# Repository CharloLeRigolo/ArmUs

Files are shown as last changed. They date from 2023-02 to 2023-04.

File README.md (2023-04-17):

# Table of content
- [ArmUs](#armus)
- [Accessing documentation](#accessing-documentation)
- [Setup](#setup)
  * [Setting up your environement (software)](#setting-up-your-environement-software)
  * [Material (Software side)](#material-software-side)
  * [Material and assembly](https://github.com/CharloLeRigolo/arm_us/tree/main/Mechanics)
- [Running the robot](#running-the-robot)
- [ROS information](#ros-information)
  * [General picture](#general-picture)
  * [Packages](#packages)
  * [Launch files](#launch-files)
  * [Config files](#config-files)
  * [Msg, srv and action files](#msg-srv-and-action-files)
- [License](#license)

# ArmUs
ArmUs is a 5 axis robot made to reproduce movement and goemetry of a real human arm. It's made by a team of 6 sherbrooke university undergraduates. The goal is to eventually add a robotic hand at the end and be able to control the whole arm-hand assembly by moving your arm. 

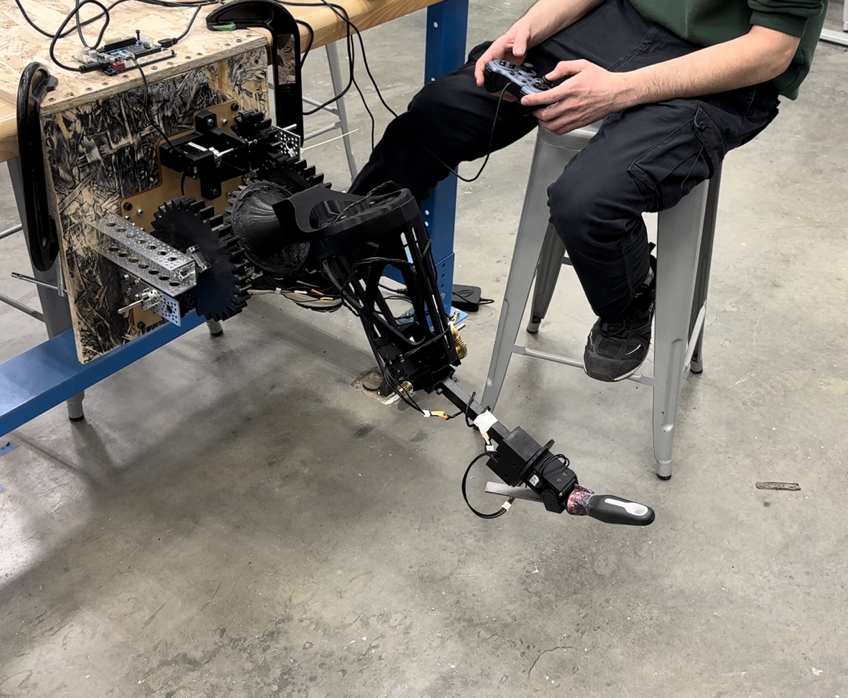
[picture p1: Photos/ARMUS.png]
ARM US


At this stage, the arm can be controled either in joint or in cartisian mode and can be visualized and calibrated in real time, it also supports software protection, torque limiters to reduce risks and a simulation mode for test purposes.

Control interface (HMI)
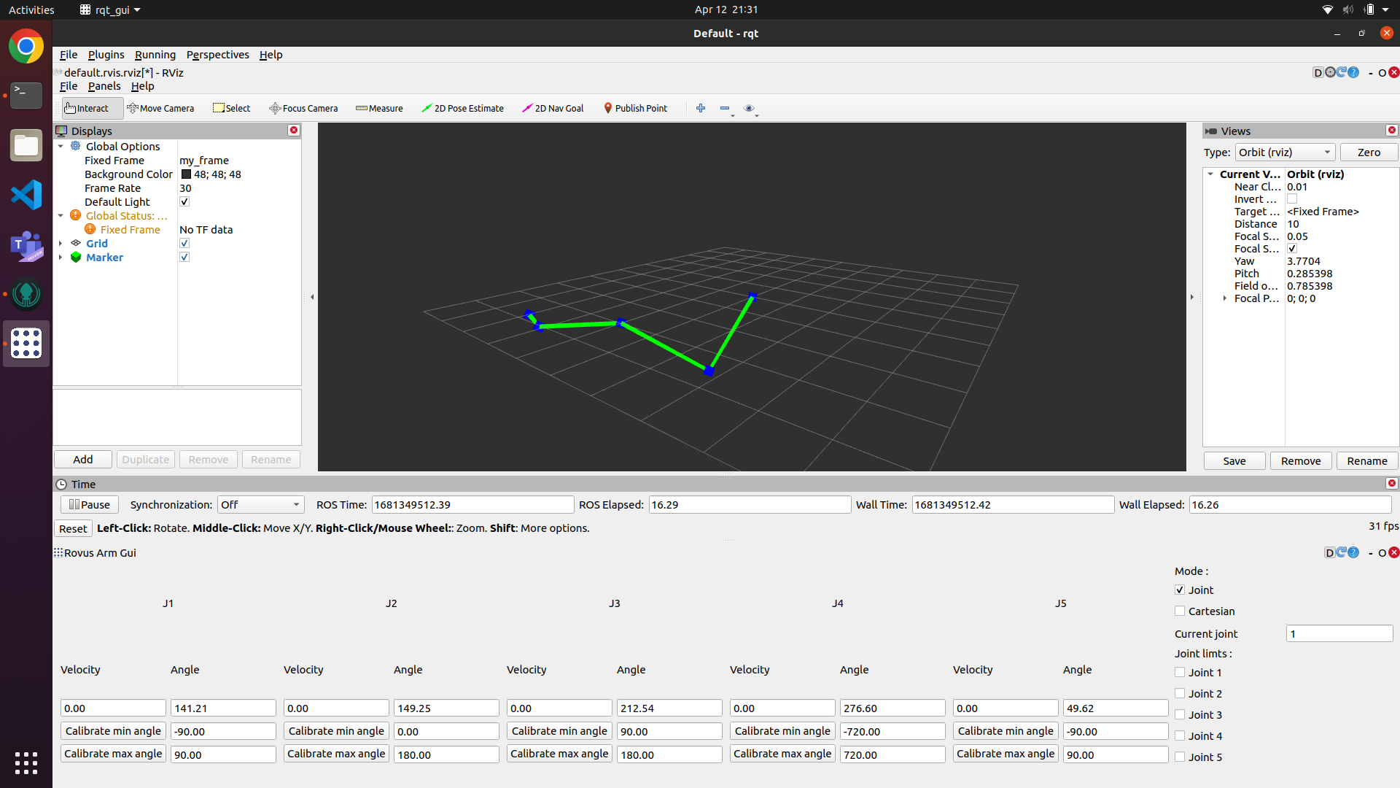
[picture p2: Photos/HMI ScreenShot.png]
HMI


# Accessing documentation
To open a package's documentation, open the index.html file found in it's "/doc" folder in your browser.
Ex:
```
firefox ~/catkin_ws/src/arm_us/arm_us/doc/html/index.html
```

# Setup
## Setting up your environement (software)
1.  Start by installing [ubuntu 20.04 desktop Focal Fossa](https://releases.ubuntu.com/focal/) on your machine (VM or dualboot), dualboot is highly recommended.
2.  Install ROS-Noetic by following [this tutorial](http://wiki.ros.org/noetic/Installation/Ubuntu)
3.  Edit your bashrc
    - Open your .bashrc (if you're using bash) 
      ```
      sudo nano ~/.bashrc
      ```
    - Then add these lines at the end
      ```
      source /opt/ros/noetic/setup.bash
      source ~/catkin_ws/devel/setup.bash
      ```
    - Save and exit
      ```
      ctrl+s
      ctrl+x
      ```
4.  Setup your catkin_ws by following [this tutorial](http://wiki.ros.org/ROS/Tutorials/InstallingandConfiguringROSEnvironment)
5.  Clone all the arm_us packages from this git repo to your catkin_ws/src folder
    - arm_us
    - arm_us_graph
    - gui_arm_us
    - arm_us_msg

6.  Install all the dependencies:
    - Dependencies
      - joy
      - dynamixel_sdk
      - dynamixel_interface

    - Run these commands to install packages available in rosdep:
      ```
      sudo apt install ros-noetic-joy
      ```

    - Some packages need to be cloned directly from GitHub as they aren't maintained in rosdep, to clone them,
      - first make */catkin_ws/src/* your working directory:
        ```
        cd ~/catkin_ws/src
        ```
      - Then, enter these commands to clone the packages:
        ```
        git clone https://github.com/csiro-robotics/dynamixel_interface.git
        git clone https://github.com/ROBOTIS-GIT/DynamixelSDK.git
        ```
    - Once all dependencies are installed, don't forget to compile your workspace
      ```
      cd ~/catkin_ws/
      catkin_make
      ```
7. Setup your OpenCR in bridge mode
	1. Install [ArduinoIDE](https://www.arduino.cc/en/software) on a computer
	2. Follow the steps in section 4.X (depending on your operating system) of the [ROBOTIS e-Manual for OpenCR](https://emanual.robotis.com/docs/en/parts/controller/opencr10/)
	3. Select the OpenCR board in ArduinoIDE
	4. Select "usb_to_dxl" In *File -> Examples -> OpenCR -> 10. Etc -> usb_to_dxl*
	5. Upload the example to the OpenCr board, make sure you're on the correct port and the device in /dev/ttyXXX has read/write access
		```
		sudo chmod a+rw /dev/ttyACM0
		```
	The OpenCR board is now in bridge mode. We will be able to control it directly from the Serial Port

## Material (Software side)
For the robot's assembly, follow the [README.md](https://github.com/CharloLeRigolo/arm_us/blob/main/Mechanics/README.md) in [/Mechanics](https://github.com/CharloLeRigolo/arm_us/tree/main/Mechanics).

- 1 OpenCR board
- 1 OpenCR 120VAC to 12VDC powersupply
- 2 Dynamixel XL430 motors
- 3 Dynamixel XM430 motors
- 1 USB micro B to USB A
- 1 Generic controller (any controller compatible with [joy](http://wiki.ros.org/joy) will work, you'll probably need to remap the keybindings if you're not using a logitech controller, in [/arm_us/config/controller_config.yaml](https://github.com/CharloLeRigolo/arm_us/blob/main/arm_us/config/controller_config.yaml)

# Running the robot
Open a terminal and launch the first launchfile:
```
roslaunch arm_us 1_interface.launch
```
This will start the HMI and the communication with the motors.
Calibrate the robot by following this [guide](https://github.com/CharloLeRigolo/arm_us/tree/main/arm_us/README.md).

Once ArmUs is calibrated, launch the 2nd launchfile
```
roslaunch arm_us 2_control.launch
```
This will enable the torque on the motors and enable the control with the controller, you should now be able to control the motors with your controller in joint or cartesian as you wish (see [keybinding]https://github.com/CharloLeRigolo/arm_us/blob/main/Photos/Keybindings%20Cartesian%20(En).PNG)

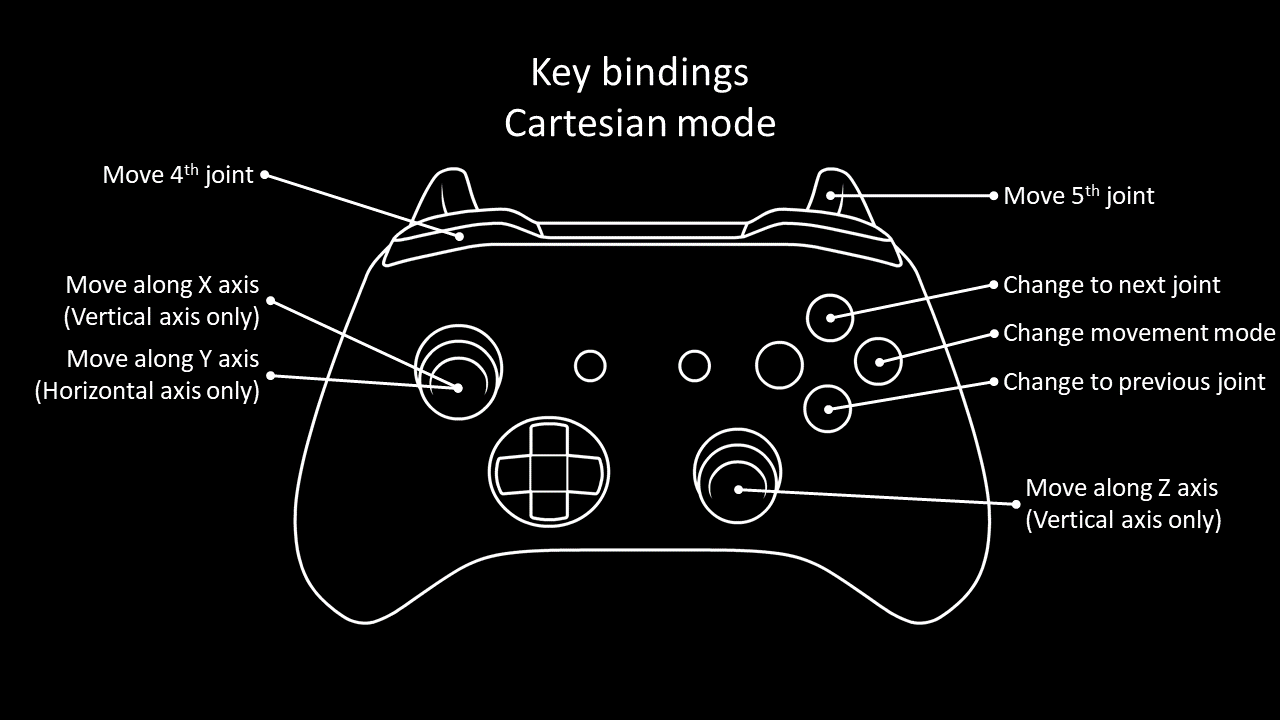
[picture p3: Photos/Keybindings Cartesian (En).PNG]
Joint control


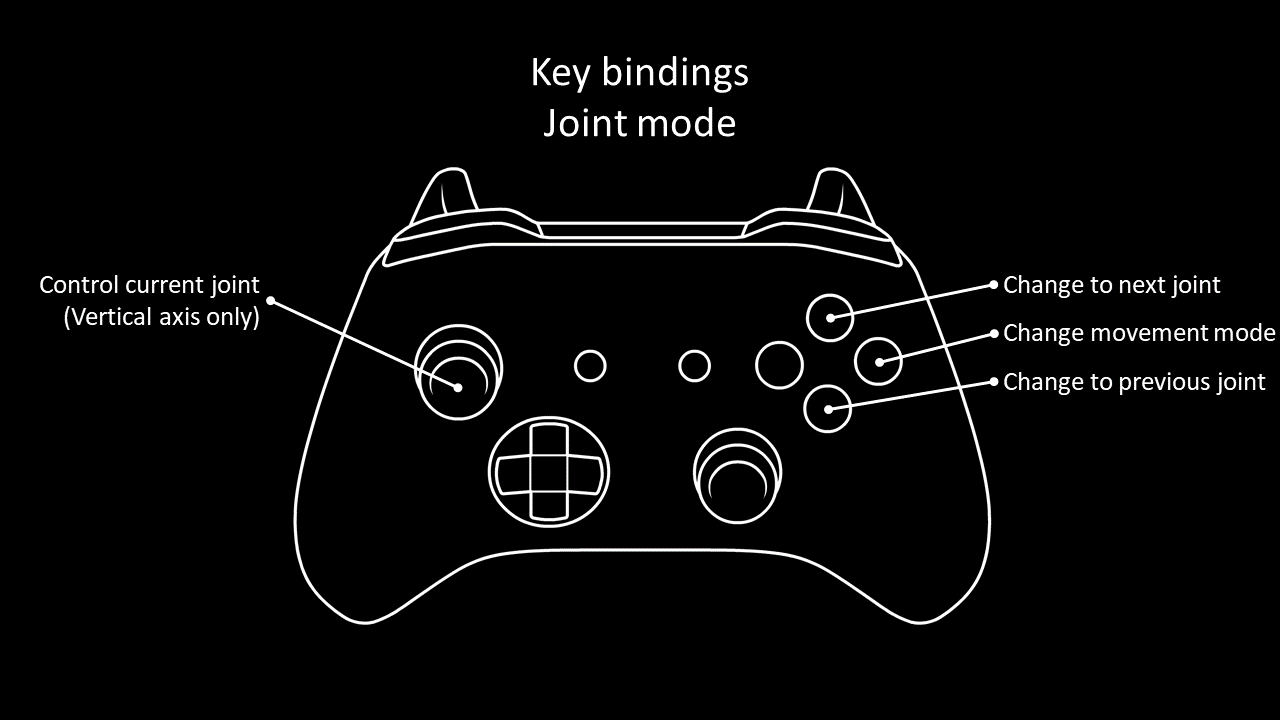
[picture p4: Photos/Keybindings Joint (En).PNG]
Cartesian control


Before killing your node, if you want to keep your calibration values, run this command
```
rosparam dump **yourpath**/calib.yaml
```
and copy the lines under "motor_translator:" in the config file arm_us/config/joint_limit.yaml.

# ROS information
## General picture
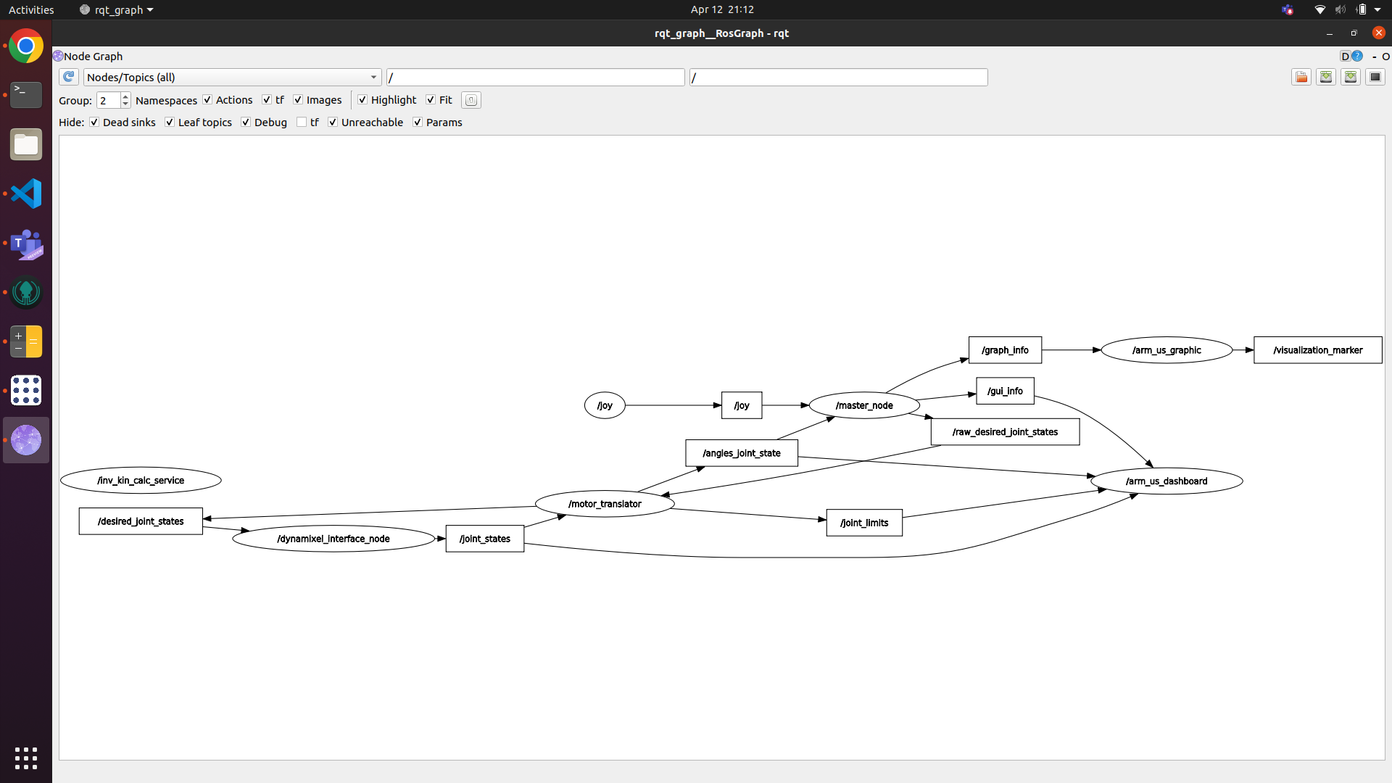
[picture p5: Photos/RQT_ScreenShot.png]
rqt_graph

## Packages
There are 4 packages in ArmUs:
 - [arm_us](https://github.com/CharloLeRigolo/arm_us/blob/main/arm_us/doc/manifest.yaml)
 - [arm_us_graph](https://github.com/CharloLeRigolo/arm_us/blob/main/arm_us_graph/doc/manifest.yaml)
 - [gui_arm_us](https://github.com/CharloLeRigolo/arm_us/blob/main/gui_arm_us/doc/manifest.yaml)
 - [arm_us_msg](https://github.com/CharloLeRigolo/arm_us/blob/main/arm_us_msg/doc/manifest.yaml)

## Launch files
- 1_interface.launch
	- Nodes:
		- motor_controller
		- motor_translator
		- rqt
		
- 2_control.launch
	- Param:
		- Verbose
		- Simulation
		- Controller
		
	- Nodes:
		- master_node
		- joy_node
		- arm_us_graphic
		
	- Service:
		- inv_kin_calc_service

## Config files
- [controller_config.yaml](https://github.com/CharloLeRigolo/arm_us/blob/main/arm_us/config/controller_config.yaml)
	- Keybindings for joy
- [joint_limit.yaml](https://github.com/CharloLeRigolo/arm_us/blob/main/arm_us/config/joint_limit.yaml)
	- Used for angle calibration and joint limit angles
- [motor_config.yaml](https://github.com/CharloLeRigolo/arm_us/blob/main/arm_us/config/motor_config.yaml)
	- Dynamixel configuration; torque limit, speed limit, motor id, etc

## Msg, srv and action files
Information for msg, srv and action files can be found directly in the [arm_us_msg](https://github.com/CharloLeRigolo/arm_us/tree/main/arm_us_msg) package

- Messages
  - [GraphInfo.msg](https://github.com/CharloLeRigolo/arm_us/blob/main/arm_us_msg/msg/GraphInfo.msg)
    - Consists of an array of float64s of length 5 named angle that represents the angles of the joints in degrees
    - It is used to send the joint angles in degrees from the motor translator to the master node, where it is then sent back to the inverse kinematic service node to control the arm in cartesian mode, and to the graph node to visualize the position of the arm in real time in Rviz.

  - [GuiInfo.msg](https://github.com/CharloLeRigolo/arm_us/blob/main/arm_us_msg/msg/GuiInfo.msg)
    - Consists of an int8 named current_joint that represents the current joint controlled, and another int8 named current_mode, which represents the current movement mode.
    - It is used to send the current joint controlled and the current movement mode to the Gui node so that the user can see in real time the information.

  - [JointLimits.msg](https://github.com/CharloLeRigolo/arm_us/blob/main/arm_us_msg/msg/JointLimits.msg)
    - Consists of an array of booleans of length 5 named joint_limits that indicates if any of the joints reached their limits.
    - It is used by the motor translator to send information to the Gui to indicate if any joint limits are reached.

- Services
  - [InverseKinematicCalc.srv](https://github.com/CharloLeRigolo/arm_us/tree/main/arm_us_msg/srv)
    - Request : 
      - angles : An array of float64s of length 3 named angles that represents the current angles of the first 3 joints used in the inverse kinematic equations.
      - commands : An array of float64s of length 4 named commands that represents the velocities of the end effector of the arm in the X, Y and Z axis.
    - Response :
      - velocities : An array of float64s of length 3 that represents the velocities of the first 3 joints needed to do the cartesian movement requested.
      - singularMatrix : A boolean name singularMatrix which indicates if a singularMatrix was encountered when calculating the joint velocities.

# License
MIT [Licence](https://github.com/CharloLeRigolo/arm_us/blob/main/LICENSE)

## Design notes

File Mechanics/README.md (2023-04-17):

# ARMUS Mecanics
## BOM
The quantity of each part is indicated between parenthesis

### Wrist

3d printed parts :
- ARMUS-500-001 (x1)
- ARMUS-500-003 (x1)
- XL430-W250-T (x2)
- HN11-I101 set (x1)
- M2 x 0.4 x 6 Flat Head Countersunk Screw (x12)
- M2.5 x 0.44 x 6 Flat Head Countersunk Screw (x12)

### Forearm

3d printed parts :
- ARMUS-400-000 (x1)

### Elbow

- XM430-W350-T (x1)
- D-Shaft 1.25x6 (x2)
- Hub 0.25 (x1)
- Bore Set Screw D hub (x1)
- 24T 6mm Bore 32P Shaft Mount Pinion Gear (x1)
- 32T 1/4” Bore 32P Shaft Mount Pinion Gear (x1)

### Upper Arm

3d printed parts :
- ARMUS-203-001 (x1)
- ARMUS-203-002 (x1)
- ARMUS-203-003 (x1)
-------------------------------------------
## SolidWorks Nomenclature
 ARMUS-000-000 --> [Principal assembly](#principal-assembly)   
 ARMUS-100-000 --> [Shoulder assembly](#shoulder-assembly)      
 ARMUS-200-000 --> [Upper Arm assembly](#upper-arm-assembly)   
 ARMUS-300-000 --> [Elbow assembly (merged to Upper Arm)](#elbow-assembly)     
 ARMUS-400-000 --> [Forearm assembly](#forearm-assembly)     
 ARMUS-500-000 --> [Wrist assembly](#wrist-assembly)      
 ***In assembly files , each piece that starts by the name ARMUS is a piece that was designed by the team ARMUS and needs to be 3D printed in PLA(Infill specified in each assembly) for the Assembly(other pieces are from other 
suppliers)***    

## Principal Assembly
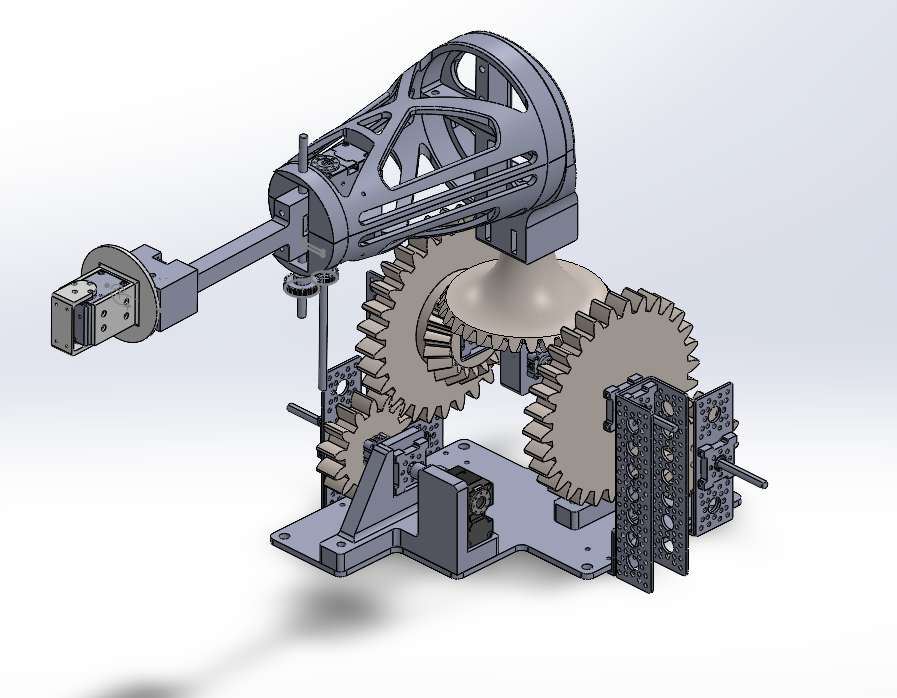
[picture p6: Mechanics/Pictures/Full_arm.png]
    
The full assembly of the arm consists of 3 parts: the Shoulder, the Upper Arm and the wrist. Each of those parts are assembled separately before doing the final assembly.  
<br/>  
[](https://www.youtube.com/watch?v=gpFWE8whwUc&ab_channel=CharlesB%C3%A9langer)

## Shoulder assembly
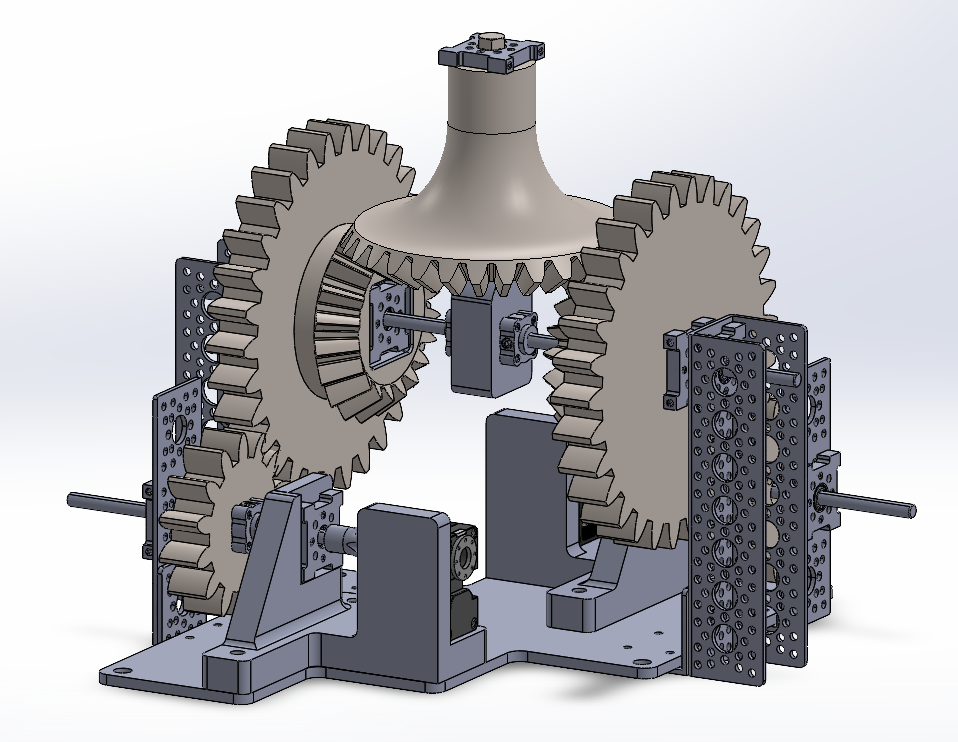
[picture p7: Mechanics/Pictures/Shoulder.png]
    
The shoulder is the main part of Armus. Most of the work is done by this part. The first thing to assemble should be the acrylic base with the shafts support. After that, bolt the two motor supports to the main support.
Afterwards, put the motor on the supports and plug the shaft to them along with the 14 teeth gear. The next step is to place the long shaft with the two big gears and the little box to put the bolt passing through the bevel gear. Afterwards, put the bevel gear between the two main gears and tighten with a bolt that goes through the little box in the middle of the shaft.  
***PLA infill 15%-20%***      
<br/>       
[](https://www.youtube.com/watch?v=jOiOeI-D89Q&ab_channel=CharlesB%C3%A9langer)
## Upper Arm assembly
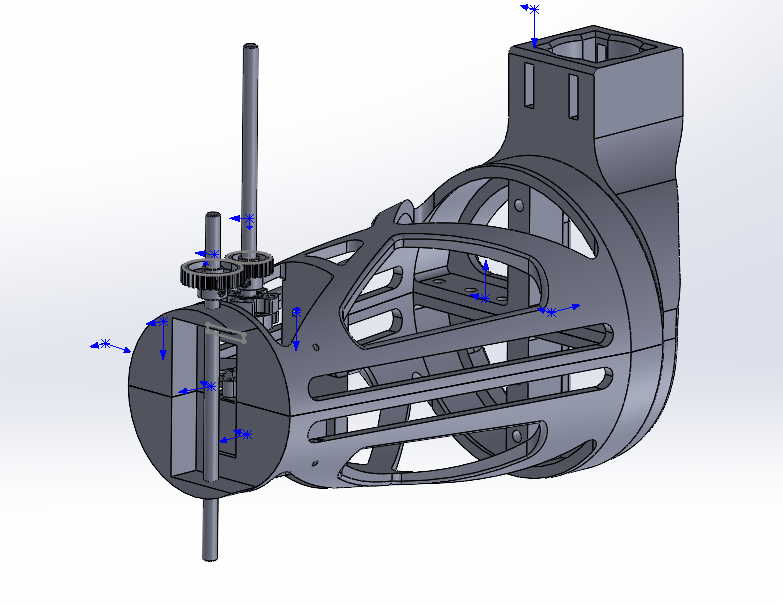
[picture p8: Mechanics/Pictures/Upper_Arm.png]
   
The Main three parts to assemble are the two parts of the humerus and the L part(the L part is the part that will be linked to the shoulder in the final assembly). Afterwards, you can mount the motor inside the humerus with the shaft and pass it through the shaft support. Finally, put the 16 teeth gear on the shaft.    
***PLA infill 10%-15%***      
<br/>   
[](https://www.youtube.com/watch?v=L0l4oxc8IDY&ab_channel=CharlesB%C3%A9langer)

## Elbow assembly 
plot       
For the elbow joint you can take a 6 inch shaft and pass is through the forearm and the humerus and add a gear on it.  
<br/>   

[](https://www.youtube.com/watch?v=L0l4oxc8IDY&ab_channel=CharlesB%C3%A9langer)

## Forearm assembly
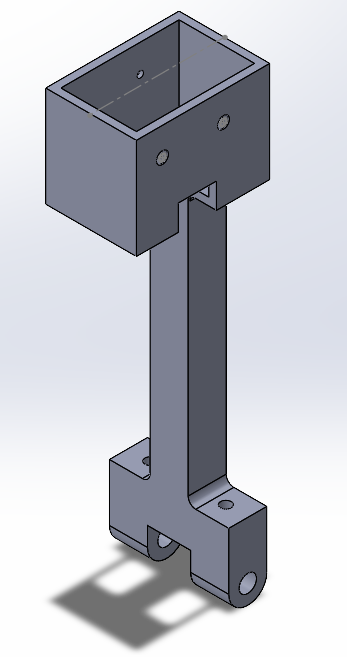
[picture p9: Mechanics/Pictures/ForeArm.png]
     
The forearm will be plugged on the elbow joint and the wrist will be put inside the motor container of the forarm.  
***PLA infill 5%-10%*** 
## Wrist assembly
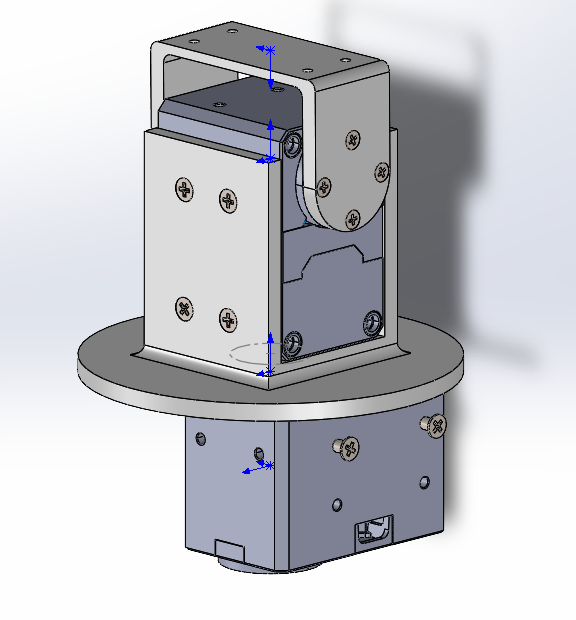
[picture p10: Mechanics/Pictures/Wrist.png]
   
The Wrist contains two motors. You can start by screwing the hand support to the first motor (We will name it number 1). Afterwards, screw the second motor(We will name it number2) underneath the motor number 1's support. Next you can bolt the motor number 1 inside its support.  
***PLA infill 5%-10%***           
<br/>   
[](https://www.youtube.com/watch?v=1WSG9IROkbA&ab_channel=CharlesB%C3%A9langer)

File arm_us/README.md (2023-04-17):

# Calibration Guide

It is necessary to calibrate the arm for accurate cartesian movements

1. Start the 1_interface.launch launchfile to have access to the GUI

2. Place the arm in a position (by hand, the motor torques are disabled)

3. Write the angle in degrees to which the current joint position will be linked in the corresponding location

4. Press either the "Calibrate min angle" or "Calibrate max angle" button on the GUI

5. The process is done when the position shown in Rviz after launching 2_control.launch matches the position of the arm

5. It is possible to dump the current calibration values with the terminal command
```
rosparam dump **your_path**/**your_calibration_name**.yaml
```

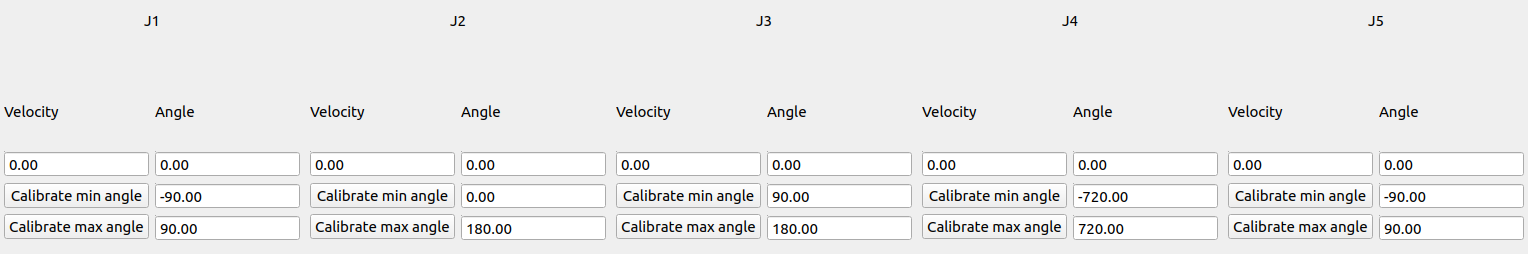
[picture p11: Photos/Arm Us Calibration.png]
Calibration


Notes :

It is not currently possible to see the position in real time of the arm while only the first launchfile is running. The code could be modified by sending the joint angles to the 3d graph node directly from the motor translator node, instead of passing by the master node.

Another workaround is to disable the joint limits in the motor translator node, and also start the 2_control.launch launchfile. It is then possible to see the position the program thinks the arm is in, while also moving the arm freely with the controller. If the joint limits are not disable, and some joint limits are off, then it might be impossible to move the arm to the desired positions to do the proper calibration.

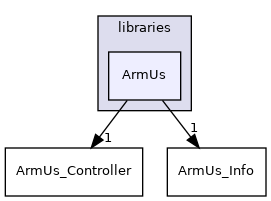
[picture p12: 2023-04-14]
arm_us/doc/html/dir_85c43fde807b09307b9d70d0642e38e7_dep.png

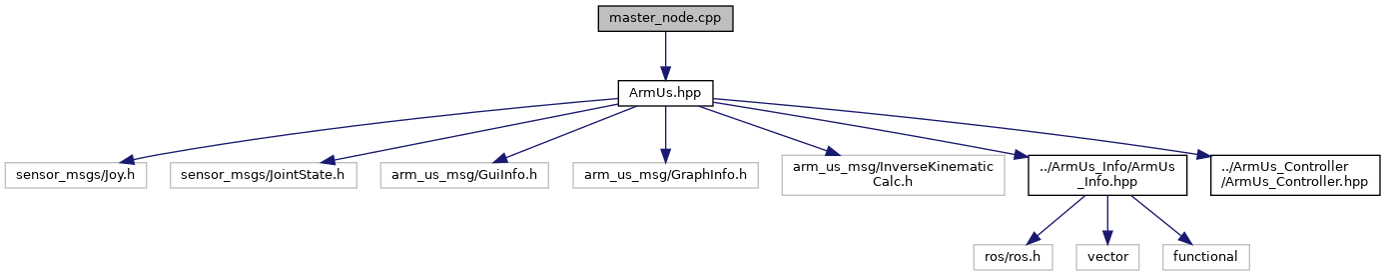
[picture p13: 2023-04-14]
arm_us/doc/html/master__node_8cpp__incl.png

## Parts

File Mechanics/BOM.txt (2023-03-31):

The quantity of each part is indicated between parenthesis
---------------
Wrist
---------------
3d printed parts :
- ARMUS-500-001 (x1)
- ARMUS-500-003 (x1)

- XL430-W250-T (x2)
- HN11-I101 set (x1)
- M2 x 0.4 x 6 Flat Head Countersunk Screw (x12)
- M2.5 x 0.44 x 6 Flat Head Countersunk Screw (x12)

---------------
Forearm
---------------
3d printed parts :
- ARMUS-400-000 (x1)

---------------
Elbow
---------------
- XM430-W350-T (x1)
- D-Shaft 1.25x6 (x2)
- Hub 0.25 (x1)
- Bore Set Screw D hub (x1)
- 24T 6mm Bore 32P Shaft Mount Pinion Gear (x1)
- 32T 1/4” Bore 32P Shaft Mount Pinion Gear (x1)

---------------
Upper Arm
---------------
3d printed parts :
- ARMUS-203-001 (x1)
- ARMUS-203-002 (x1)
- ARMUS-203-003 (x1)

---------------
Shoulder
---------------
3d printed parts :
- ARMUS-103-002 (x2)
- ARMUS-103-003 (x1)
- ARMUS-103-004 (x1)
- ARMUS-103-200 (x1)
- ARMUS-103-301 (x2)
- ARMUS-103-400 (x1)
- ARMUS-103-500 (x2)

Laser-cut parts :
- ARMUS-103-001 cut in acrylic (x1)

- XM430-W350-T (x2)
- Bore Side Tapped Pillow Block 1.25 (x12)
- Bore Set Screw D hub (x4)
- Hub 0.25 (x1)
- Hnut 0.2500-20-D-N (x1)
- Hbolt 0.2500-20x4.5x0.75-N
- 6" Aluminum Channel (x2)
- Flat Triple Channel Bracket (x2)
- 90 Degree Single Angle Channel Bracket (x4)
- D-Shaft 1.25x6 (x2)
- D-Shaft 1.25x8 (x1)

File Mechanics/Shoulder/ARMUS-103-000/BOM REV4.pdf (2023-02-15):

DOCUMENT PREVIEW | ITEM NO. | PART NUMBER | DESCRIPTION | QTY.
1 | ARMUS-REV4-400 | 1
2 | ARMUS-REV4-301 | 2
3 | ARMUS-REV4-500 | 2
4 | ARMUS-REV4-005 | 2

5

Bore Side Tapped
Pillow Block 1.25 | 10
6 | ARMUS-REV4-006 | 4
7 | ARMUS-REV4-007 | 2
8 | ARMUS-REV4-200 | 1

9

bore_set_screw_D_hu
b

2

10 | D-Shaft 1.25x8 | 1

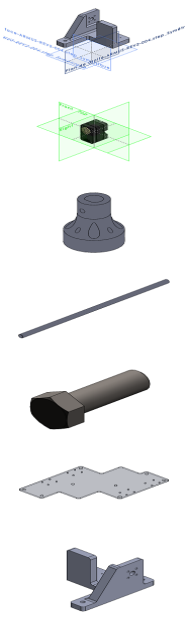
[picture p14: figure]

11 | ARMUS-REV4-004 | 1
12 | XM430-W350-R | 2
13 | ARMUS-REV4-002 | 2
14 | D-Shaft 1.25x6 | 2
15 | HBOLT 0.2500-
20x4.5x0.75-N | 1
16 | ARMUS-REV4-001_V2 | 1
17 | ARMUS-REV4-003 | 1

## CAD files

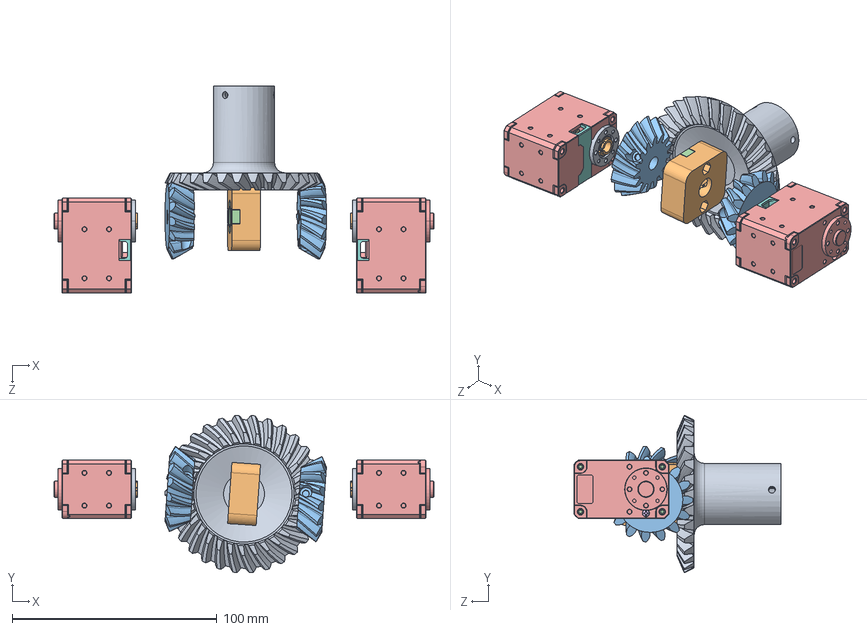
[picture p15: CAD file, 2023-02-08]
Mechanics/Shoulder/ARMUS-100-000/ARMUS-100-000.SLDASM
185.8 x 77.0 x 101.4 mm
ARMUS-100-001
ARMUS-100-002
ARMUS-100-003 x 2
ARMUS-100-004
DC11_A01_DUMMY.stp x 2
DX124_SCREW-COVER.stp x 2
B3B-EH.stp x 4
DC11_A01_CASE_CVR_DUMMY.stp x 2
DC11_A01_IDLER_DUMMY.stp x 2
DC11_A01_IDLER_CAP_DUMMY.stp x 2
DC11_A01_IDLER_SCREW.stp x 2
FHS_M2_5X10.stp x 16
DC11_A01_SPACER_DUMMY.stp x 16

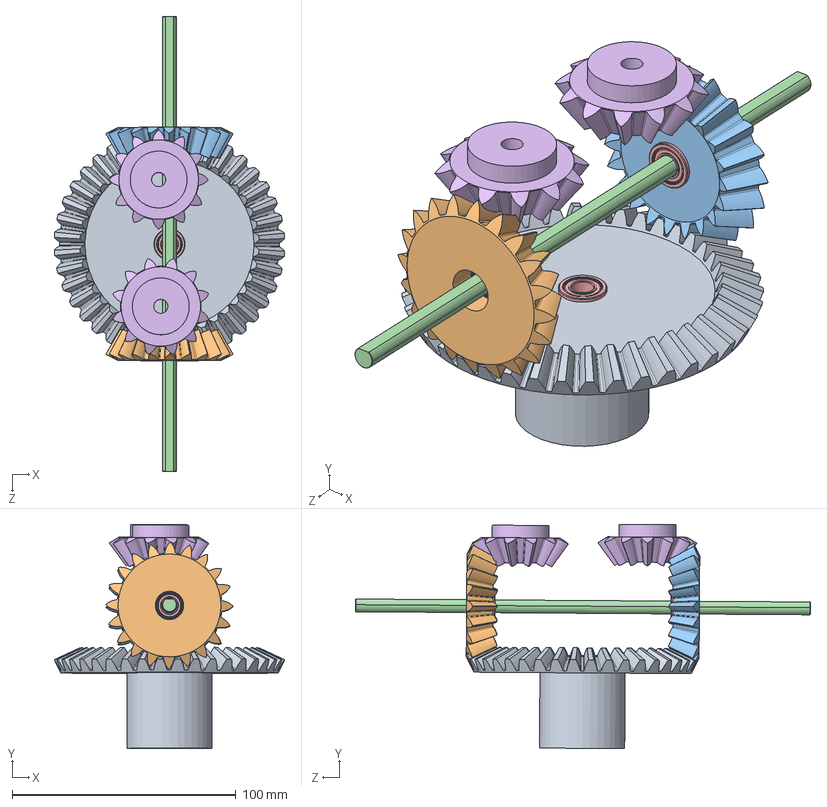
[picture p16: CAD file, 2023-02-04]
Mechanics/Shoulder/ARMUS-100-000/ARMUS-200-000/ARMUS-200-000.SLDASM
103.0 x 100.2 x 203.2 mm
ARMUS-200-001
ARMUS-200-002
straight bevel pinion_ai
ARMUS-200-003.step
ARMUS-200-004.step x 3
straight bevel gear_ai x 2

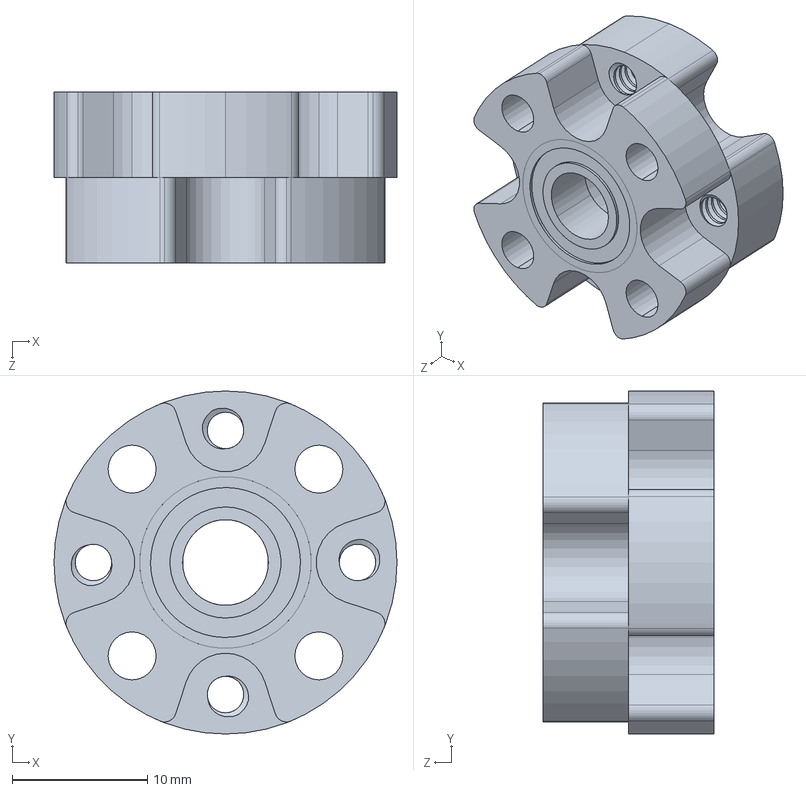
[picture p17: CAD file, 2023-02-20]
Mechanics/Shoulder/ARMUS-102-000/ARMUS-REV2-200.SLDASM
25.4 x 25.4 x 12.7 mm

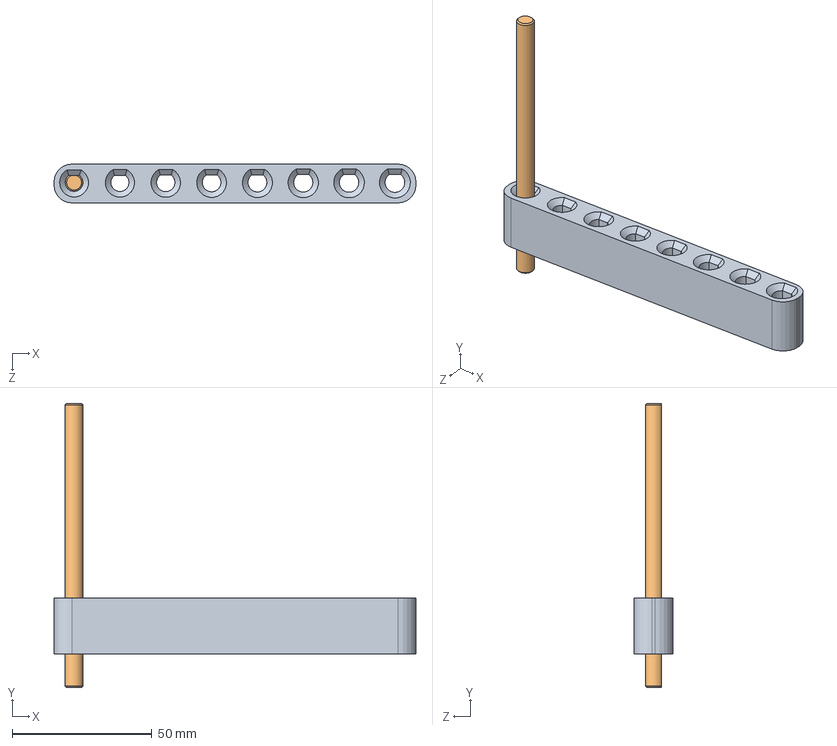
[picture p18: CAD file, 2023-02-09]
Mechanics/Shoulder/test_shaft/Assemblage_test.SLDASM
129.4 x 101.6 x 13.9 mm

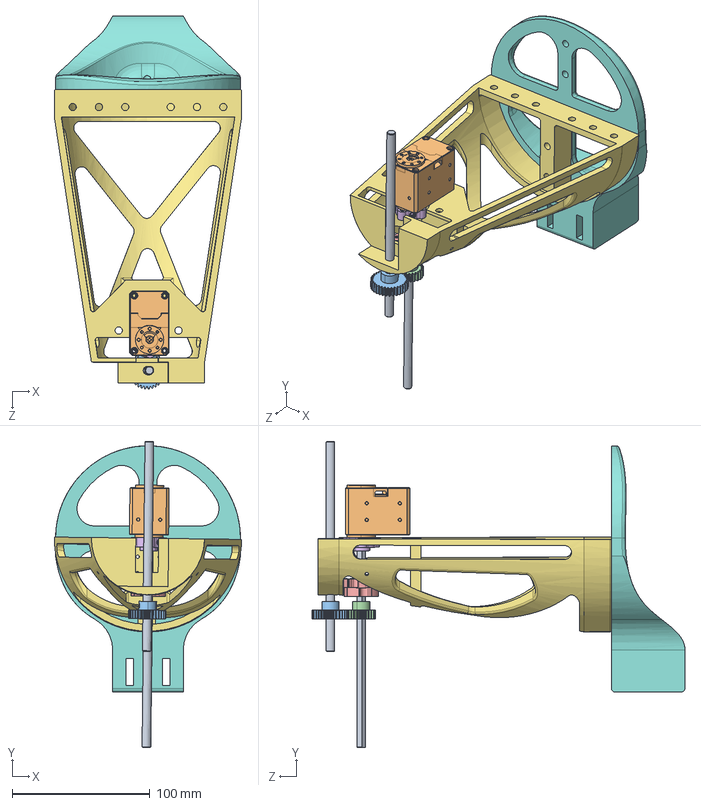
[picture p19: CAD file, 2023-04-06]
Mechanics/Upper Arm/ARMUS-203-000/ARMUS-203-000.SLDASM
135.8 x 222.3 x 270.5 mm
D-Shaft 1.25x6 x 2
ARMUS-200-004
Pignon 32T
Pignon 24T
HUB-0_25
bore_set_screw_D_hub
ARMUS-203-002
ARMUS-203-003

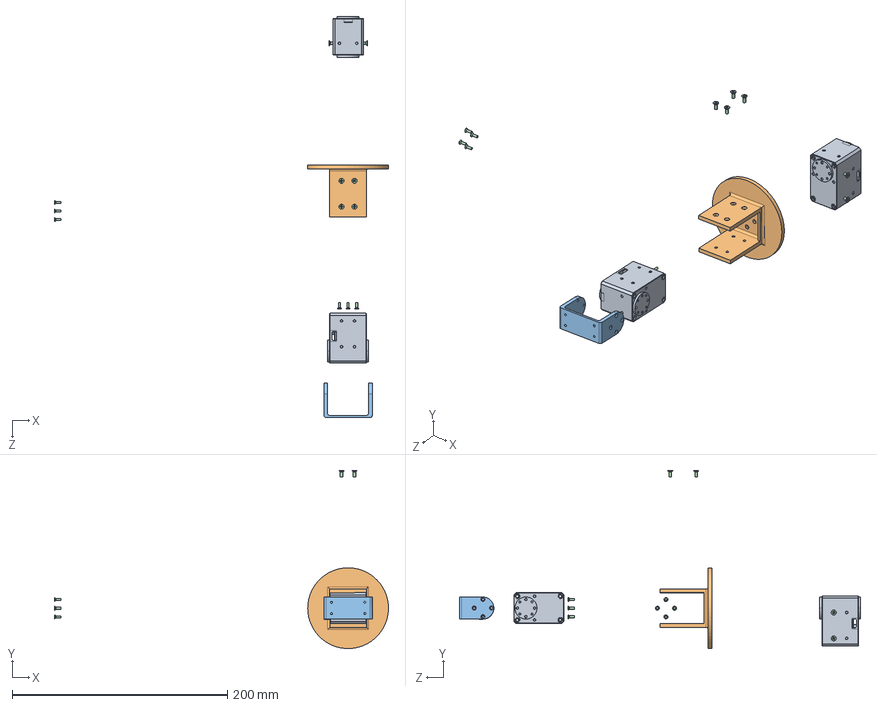
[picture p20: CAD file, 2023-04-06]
Mechanics/Wrist/ARMUS-500-000.SLDASM
310.0 x 165.3 x 372.6 mm
ARMUS-500-002 x 2
ARMUS-500-001
ARMUS-500-003
flat head screw_am x 16

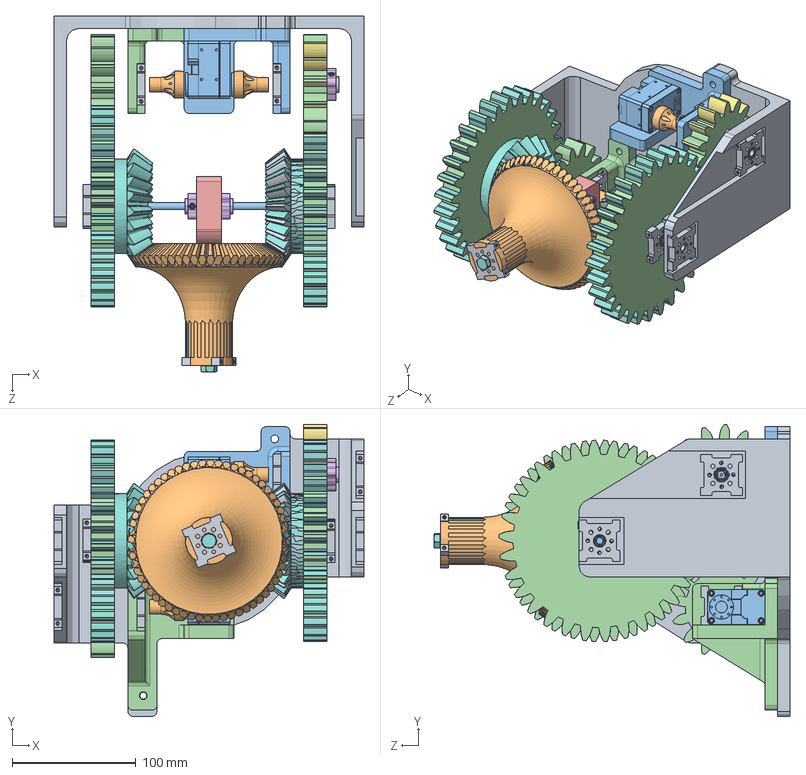
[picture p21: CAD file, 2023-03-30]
Mechanics/Shoulder/ARMUS-101-000/Support Modulaire/ARMUS-REV2-000.SLDASM
250.0 x 235.5 x 287.1 mm
ARMUS-REV2-001
ARMUS-REV2-002 x 2
ARMUS-REV2-004
ARMUS-REV2-005
ARMUS-REV2-201
HUB-0_25
hex nut_ai
ARMUS-REV2-301 x 2
Bore Side Tapped Pillow Block 1.25 x 12
ARMUS-REV2-401
XM430-W350-R x 2
spur gear_ai x 2
hex screw_am x 8
bore_set_screw_D_hub x 3
ARMUS-REV2-501
hex bolt_ai
D-Shaft 1.25x8

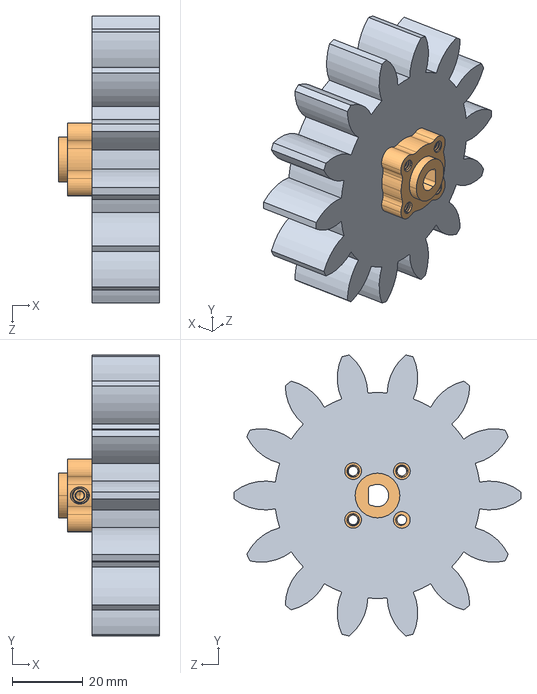
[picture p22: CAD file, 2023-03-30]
Mechanics/Shoulder/ARMUS-103-000/ARMUS-103-500.SLDASM
28.6 x 79.7 x 81.3 mm
ARMUS-REV4-501
bore_set_screw_D_hub

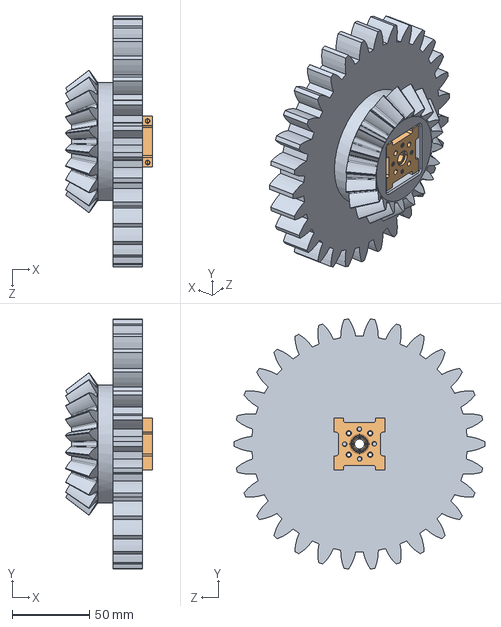
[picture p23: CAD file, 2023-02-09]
Mechanics/Impression/ARMUS-REV2-300.SLDASM
56.2 x 162.0 x 162.5 mm
ARMUS-REV2-100
Bore Side Tapped Pillow Block 1.25 x 2

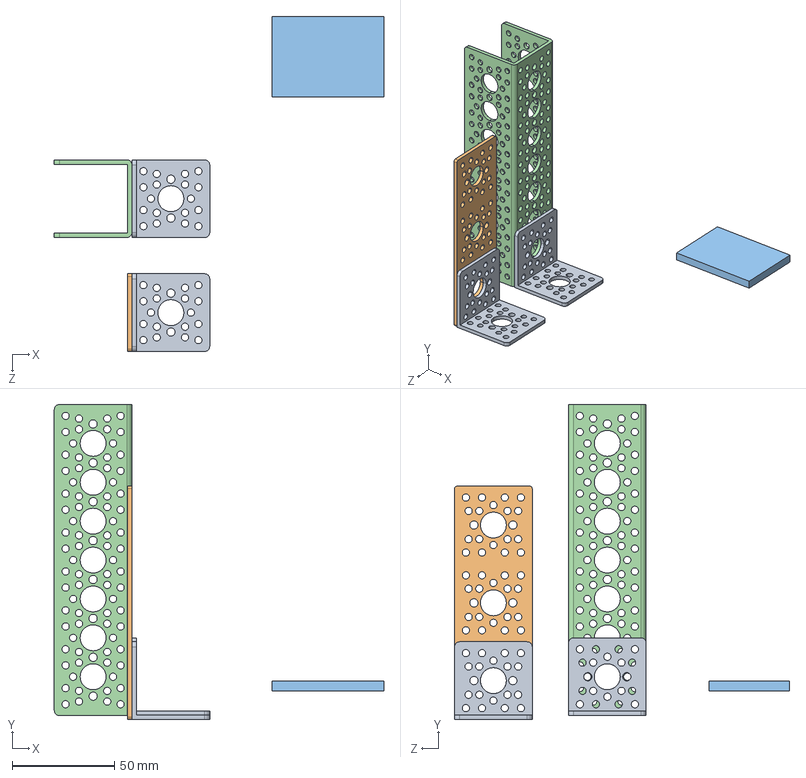
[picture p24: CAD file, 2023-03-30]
Mechanics/Shoulder/ARMUS-101-000/Support Modulaire/ARMUS-REV2-600.SLDASM
161.4 x 154.3 x 164.1 mm
ARMUS-REV2-010 x 2
ARMUS-REV2-011
ARMUS-REV2-013
ARMUS-REV2-012

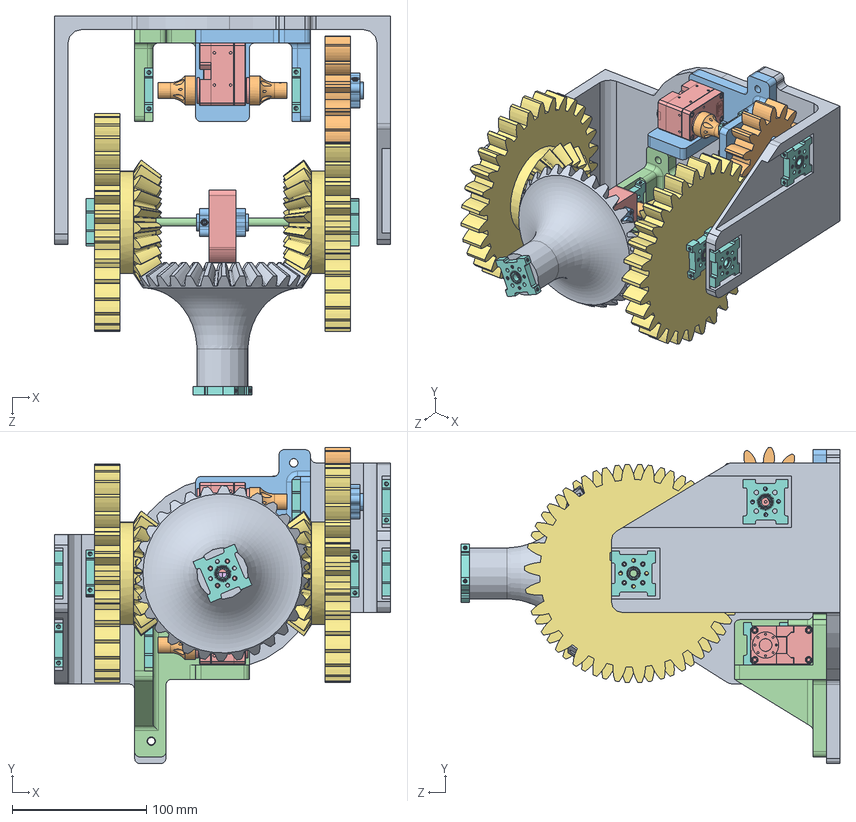
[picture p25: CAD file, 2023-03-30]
Mechanics/Shoulder/ARMUS-101-000/ARMUS-101-000.SLDASM
250.0 x 235.5 x 281.8 mm
ARMUS-101-001
ARMUS-101-002 x 2
ARMUS-101-004
ARMUS-101-005
ARMUS-101-201
HUB-0_25
ARMUS-REV2-301 x 2
Bore Side Tapped Pillow Block 1.25 x 12
ARMUS-REV2-401
ARMUS-REV2-501
bore_set_screw_D_hub x 3
D-Shaft 1.25x8
XM430-W350-R x 2

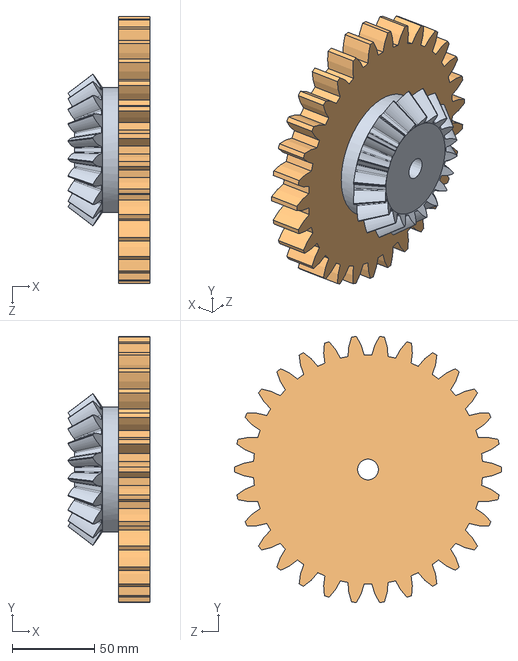
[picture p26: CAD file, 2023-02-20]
Mechanics/Shoulder/ARMUS-102-000/ARMUS-REV2-100.SLDASM
49.8 x 162.0 x 162.5 mm
straight bevel pinion_ai
spur gear_ai

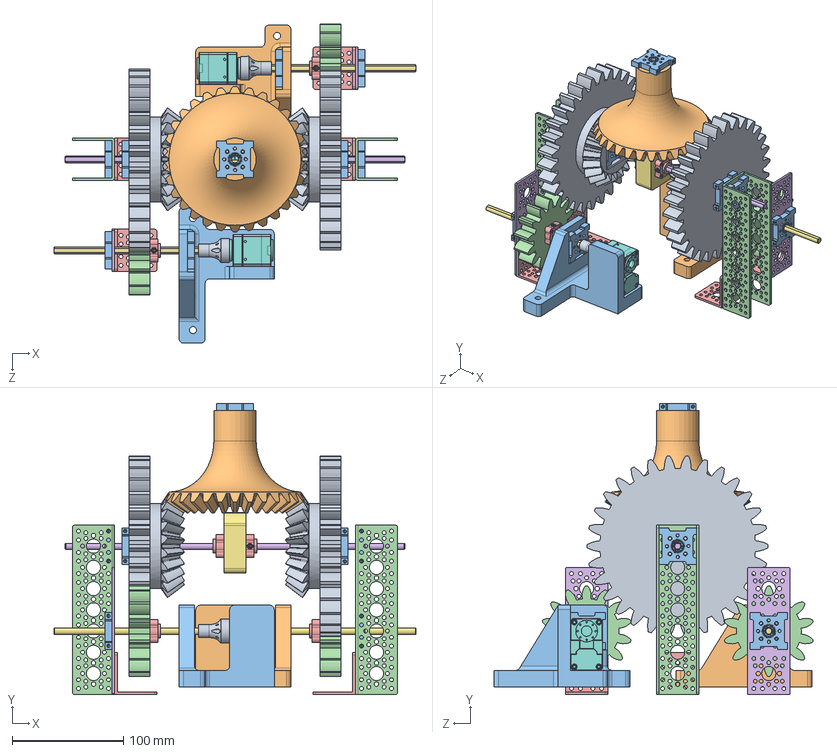
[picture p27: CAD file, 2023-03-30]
Mechanics/Shoulder/ARMUS-103-000/ARMUS-103-000.SLDASM
324.9 x 261.6 x 286.6 mm
ARMUS-103-002 x 2
ARMUS-103-003
ARMUS-103-004
ARMUS-103-005 x 2
ARMUS-103-006 x 4
ARMUS-103-007 x 2
ARMUS-REV4-201
HUB-0_25
ARMUS-103-301 x 2
ARMUS-REV4-401
Bore Side Tapped Pillow Block 1.25 x 12
ARMUS-REV4-501 x 2
bore_set_screw_D_hub x 4
D-Shaft 1.25x8
D-Shaft 1.25x6 x 2
XM430-W350-R x 2

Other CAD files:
Mechanics/Shoulder/ARMUS-103-000/ARMUS-103-200.SLDASM
Mechanics/Shoulder/ARMUS-101-000/ARMUS-101-200.SLDASM
Mechanics/Shoulder/ARMUS-test-000/Shoulder/ARMUS-REV4-200.SLDASM
Mechanics/Shoulder/ARMUS-101-000/ARMUS-REV2-100.SLDASM
Mechanics/Shoulder/ARMUS-102-000/ARMUS-REV2-500.SLDASM
Mechanics/Forearm/ARMUS-400-000.SLDPRT
Mechanics/Forearm/STL/ARMUS-400-000.STL
Mechanics/Impression/ARMUS-REV2-301.SLDPRT
Mechanics/Impression/STLs/Print Settings.3mf
Mechanics/REV5/Shoulder/STL_Spacers/ARMUS-REV4-003.STL
Mechanics/REV5/Shoulder/STL_Spacers/ARMUS-REV4-004.STL
Mechanics/Shoulder/ARMUS-100-000/ARMUS-100-001.SLDPRT
Mechanics/Shoulder/ARMUS-100-000/ARMUS-100-002.SLDPRT
Mechanics/Shoulder/ARMUS-100-000/ARMUS-100-002_V2.SLDPRT
Mechanics/Shoulder/ARMUS-100-000/ARMUS-100-004.SLDPRT
Mechanics/Shoulder/ARMUS-100-000/ARMUS-100-005.SLDASM
Mechanics/Shoulder/ARMUS-100-000/ARMUS-100-005.stp
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

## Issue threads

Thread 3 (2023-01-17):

Preliminary Code for Motor Control

CharloLeRigolo, 2023-01-17:

Pmichaud29, 2023-01-26:
mikael 2.5 hrs
Philippe 6.5 hrs

Pmichaud29, 2023-01-26:
Requirements :
- 2 XL430
- Ctrl : id3 with Left Joystick and id9 with Right One
- CtrlMode : Velocity mapped on joystick from 0 t max rad/s

Closed 2023-02-05.

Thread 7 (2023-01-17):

Preleminary Shoulder conception

CharloLeRigolo, 2023-01-17:

CharloLeRigolo, 2023-01-21:
First  version of SolidWork Assembly of the shoulder done

CharloLeRigolo, 2023-01-31:
reprint of some pieces

Pmichaud29, 2023-01-31:
Cadded motor to 6mm shaft coupling adapter

Heures :
0.5h

CharloLeRigolo, 2023-01-31:
New Print Started
H: 0,5h

Closed 2023-02-05.

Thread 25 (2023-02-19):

CAD elbow joint

CharloLeRigolo, 2023-02-19:

CharloLeRigolo, 2023-03-03:
1h30
cad elbow: support to add blot to the motor and adding of the gear in assembly
ToDo: adding a bering to support the shaft and the gear + adding of bering to support the second shaft (with the 32th gear) + the gear can't touch so we need to reduce the gap between the two or replace the 16th gear by a 24th gear.

CharloLeRigolo, 2023-03-07:
1h
Change of the gear 16th for a gear 24th and ajustement of the position

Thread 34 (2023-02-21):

Redo control + Add joint limits for 1 delivery

Pmichaud29, 2023-02-21:

Pmichaud29, 2023-02-21:
Heures :
  - Phil : 2h
  - Mik : 2h

Pmichaud29, 2023-03-29:
Bug fix joint limit

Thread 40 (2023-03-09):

Add 2nd accel + flex sensor to sleeve

Pmichaud29, 2023-03-09:

Pmichaud29, 2023-03-09:
Phil : 8h

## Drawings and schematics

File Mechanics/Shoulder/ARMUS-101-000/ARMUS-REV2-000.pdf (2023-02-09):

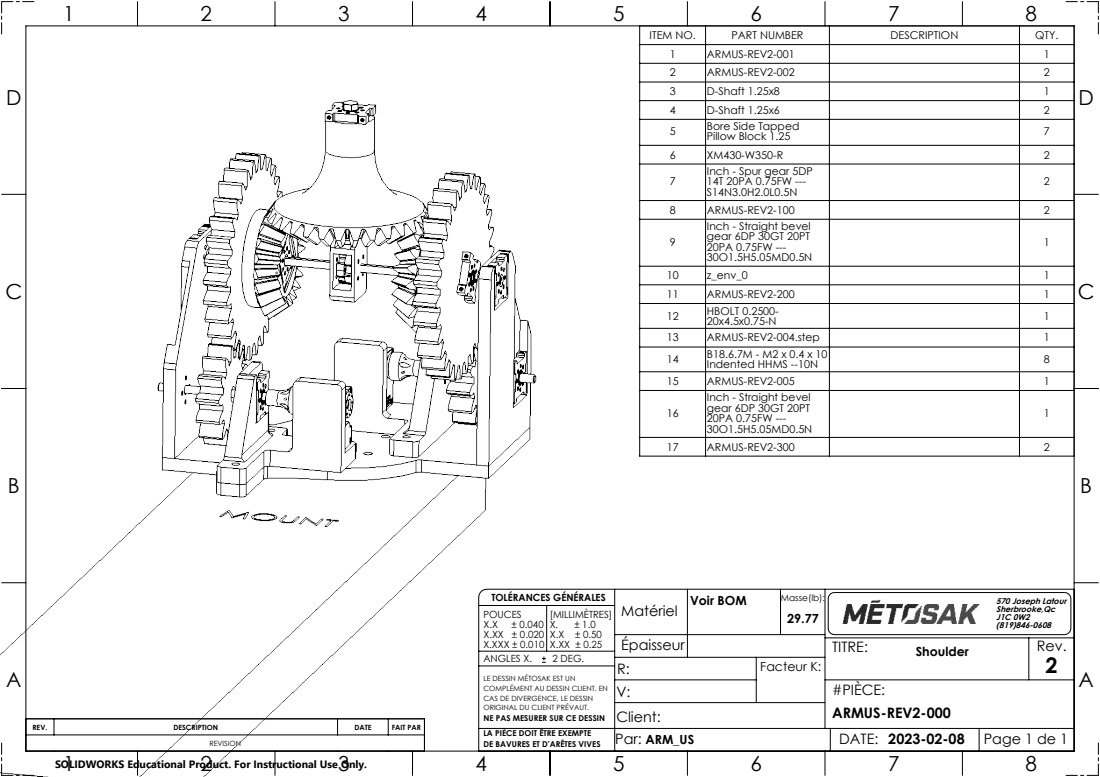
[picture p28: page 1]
REV.; DESCRIPTION; DATE; FAIT PAR; X.X ± 0.040 X.XX ± 0.020 X.XXX ± 0.010; TOLÉRANCES GÉNÉRALES; 570 Joseph Latour; Voir BOM; ANGLES X.; 2 DEG.

ITEM NO. | PART NUMBER | DESCRIPTION | QTY.
1 | ARMUS-REV2-001 | | 1
2 | ARMUS-REV2-002 | | 2
3 | D-Shaft 1.25x8 | | 1
4 | D-Shaft 1.25x6 | | 2
5 | Bore Side Tapped Pillow Block 1.25 | | 7

6 | XM430-W350-R | | 2
7 | Inch - Spur gear 5DP 14T 20PA 0.75FW ---S14N3.0H2.0L0.5N | | 2

8 | ARMUS-REV2-100 | | 2
9 | Inch - Straight bevel gear 6DP 30GT 20PT 20PA 0.75FW ---30O1.5H5.05MD0.5N | | 1

10 | z_env_0 | | 1
11 | ARMUS-REV2-200 | | 1
12 | HBOLT 0.2500-20x4.5x0.75-N | | 1
13 | ARMUS-REV2-004.step | | 1
14 | B18.6.7M - M2 x 0.4 x 10 Indented HHMS --10N | | 8
15 | ARMUS-REV2-005 | | 1
16 | Inch - Straight bevel gear 6DP 30GT 20PT 20PA 0.75FW ---30O1.5H5.05MD0.5N | | 1

17 | ARMUS-REV2-300 | | 2

Épaisseur
R: | Facteur K:
V: | | #PIÈCE: ARMUS-REV2-000

TITRE: Shoulder | Rev. 2

LE DESSIN MÉTOSAK EST UN
COMPLÉMENT AU DESSIN CLIENT. EN
CAS DE DIVERGENCE, LE DESSIN
ORIGINAL DU CLIENT PRÉVAUT.
NE PAS MESURER SUR CE DESSIN
LA PIÈCE DOIT ÊTRE EXEMPTE
DE BAVURES ET D'ARÊTES VIVES

SOLIDWORKS Educational Product. For Instructional Use Only.

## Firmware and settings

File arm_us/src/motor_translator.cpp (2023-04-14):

/**
 * @file motor_translator.cpp
 * @author Mikael St-Arnaud et Philippe Michaud (stam1001, micp1402)
 * @brief This node acts as an interface between the dynamixel motor_controller and arm_us's control nodes.
 * It take raw_position value from the motors and converts them into real angles. It also applies real word
 * joint limits to sent commands (from arm_us) and add a motor speed limiter in cartesian control mode.
 * @version 0.1 
 * @date 2023-04-12
 *
 * @copyright Copyright (c) 2023 - See ARM_US licence
 */

#include "ros/ros.h"
#include "sensor_msgs/JointState.h"
#include <unordered_map>
#include "std_msgs/Header.h"
#include "std_msgs/Bool.h"
#include "arm_us_msg/JointLimits.h"

#define NB_JOINT 5                                // numbers of Joints
const std::string NODE_NAME = "motor_translator"; // used for getting rosparam with correct name

void commandCallback(const sensor_msgs::JointStateConstPtr &msg);
void stateCallback(const sensor_msgs::JointStateConstPtr &msg);
void simulateStateCallback();
void setParams();

// Global variables
ros::Publisher pub_command;
ros::Publisher pub_angles;
ros::Publisher pub_gui;

double joint_angles[NB_JOINT];
double joint_velocity[NB_JOINT];
double joint_effort[NB_JOINT];
double joint_positions[NB_JOINT]; // For simulation purposes only
bool joint_limits[NB_JOINT];
bool flag_no_connection = 0;
double max_speed;

enum class ControlMode
{
    Real = 0,
    Simulation = 1
};
ControlMode g_control_mode;

std::unordered_map<std::string, int> motor_map = {
    {"motor1", 0},
    {"motor2", 1},
    {"motor3", 2},
    {"motor4", 3},
    {"motor5", 4}};

short motor_order[5] = {0, 1, 2, 3, 4};

int main(int argc, char *argv[])
{

    ros::init(argc, argv, NODE_NAME);
    ros::NodeHandle n;

    setParams();

    ros::Subscriber sub_command = n.subscribe("raw_desired_joint_states", 1, commandCallback);
    ros::Subscriber sub_state = n.subscribe("joint_states", 1, stateCallback);

    pub_command = n.advertise<sensor_msgs::JointState>("desired_joint_states", 1);
    pub_angles = n.advertise<sensor_msgs::JointState>("angles_joint_state", 1);
    pub_gui = n.advertise<arm_us_msg::JointLimits>("joint_limits", 1);

    while (ros::ok())
    {
        if (g_control_mode == ControlMode::Simulation)
        {
            // Replace position callback from motors
            simulateStateCallback();
        }
        ros::spinOnce();
    }
}

/**
 * @brief Get's raw JointState comming from Arm_us
 * and checks joint limits and add a speed limiter
 * correction factor to keep cartesian control accurate
 *
 * @param msg
 */
void commandCallback(const sensor_msgs::JointStateConstPtr &msg)
{
    sensor_msgs::JointState cmd;
    cmd = *msg;

    // Updating parameters
    double max_angles[NB_JOINT];
    double min_angles[NB_JOINT];
    for (short i = 0; i < NB_JOINT; i++)
    {
        ros::param::get("/" + NODE_NAME + "/j" + std::to_string(i + 1) + "/max_limit", max_angles[i]);
        ros::param::get("/" + NODE_NAME + "/j" + std::to_string(i + 1) + "/min_limit", min_angles[i]);
        cmd.velocity[i] = 0.0;
    }

    // for (auto i = 0; i < 2; i++)
    // {
    //     cmd.velocity[i] = msg->velocity[i];
    // }

    // Checking other motor limits
    for (auto i = 0; i < NB_JOINT; i++)
    {
        if (i == 0)
        {
            bool increase = msg->velocity[0] > msg->velocity[1];
            if ((increase && joint_angles[i] > max_angles[i]) || (!increase && joint_angles[i] < min_angles[i]))
            {
                cmd.velocity[0] = 0.0;
                cmd.velocity[1] = 0.0;
                joint_limits[0] = true;
                // ROS_WARN("Joint #%d at limit", (i + 1));
            }
            else
            {
                cmd.velocity[0] = msg->velocity[0];
                cmd.velocity[1] = msg->velocity[1];
                joint_limits[0] = false;
                // ROS_WARN("Joint #%d at limit", (i + 1));
            }
        }
        else if (i > 1)
        {
                if ((msg->velocity[i] > 0.0 && joint_angles[i] >= max_angles[i]) || (msg->velocity[i] < 0.0 && joint_angles[i] <= min_angles[i]))
                {
                    cmd.velocity[i] = 0.0;
                    joint_limits[i] = true;
                    ROS_WARN("Joint #%d at limit", (i + 1));
                }
                else
                {
                    cmd.velocity[i] = msg->velocity[i];
                    joint_limits[i] = false;
                }

            cmd.velocity[i] = msg->velocity[i];
            joint_limits[i] = false;
        }
    }

    // ROS_WARN("Command with joint limits :");
    // ROS_WARN("m1 = %f, m2 = %f, m3 = %f, m4 = %f, m5 = %f", cmd.velocity[0], cmd.velocity[1], cmd.velocity[2], cmd.velocity[3], cmd.velocity[4]);

    // Applying speed limiter
    // NEEDS to be tested
    double cmd_max_speed = *std::max_element(std::begin(cmd.velocity), std::end(cmd.velocity));
    if (cmd_max_speed > max_speed)
    {
        double factor = max_speed / cmd_max_speed;
        for (auto i = 0; i < NB_JOINT; i++)
        {
            cmd.velocity[i] *= factor;
        }
    }

    // ROS_WARN("Command with joint limits and speed limiter :");
    // ROS_WARN("m1 = %f, m2 = %f, m3 = %f, m4 = %f, m5 = %f", cmd.velocity[0], cmd.velocity[1], cmd.velocity[2], cmd.velocity[3], cmd.velocity[4]);

    // Building and sending cmd msg
    if (g_control_mode == ControlMode::Simulation)
    {
        joint_positions[0] += cmd.velocity[0];
        joint_positions[1] += cmd.velocity[1];
        joint_positions[2] += cmd.velocity[2];
        joint_positions[3] += cmd.velocity[3];
        joint_positions[4] += cmd.velocity[4];
        // ROS_WARN("Joint positions with joint limits :");
        // ROS_WARN("m1 = %f, m2 = %f, m3 = %f, m4 = %f, m5 = %f", joint_positions[0], joint_positions[1], joint_positions[2], joint_positions[3], joint_positions[4]);
    }

    pub_command.publish(cmd);
}

/**
 * @brief Callback to translate raw position value of motor to angle
 * and reorganise msg with sorted motor order (1, 2, 3, ...)
 *
 * @param msg
 */
void stateCallback(const sensor_msgs::JointStateConstPtr &msg)
{
    sensor_msgs::JointState angle_feedback;

    int msg_size = msg->position.size();
    if ((msg_size < NB_JOINT) || (msg->position.size() != msg->effort.size()) || (msg->position.size() != msg->velocity.size()))
    {
        if (!flag_no_connection)
        {
            ROS_WARN("Lost connection to a motor, only %d motor detected", msg_size);
            flag_no_connection = 1;
        }
        return;
    }
    flag_no_connection = 0;

    double max_angles[NB_JOINT];
    double min_angles[NB_JOINT];
    double pos_max_angles[NB_JOINT];
    double pos_min_angles[NB_JOINT];

    for (short i = 0; i < NB_JOINT; i++)
    {
        ros::param::get("/" + NODE_NAME + "/j" + std::to_string(i + 1) + "/pos_max_angle", pos_max_angles[i]);
        ros::param::get("/" + NODE_NAME + "/j" + std::to_string(i + 1) + "/pos_min_angle", pos_min_angles[i]);
        ros::param::get("/" + NODE_NAME + "/j" + std::to_string(i + 1) + "/max_limit", max_angles[i]);
        ros::param::get("/" + NODE_NAME + "/j" + std::to_string(i + 1) + "/min_limit", min_angles[i]);
    }

    for (int i = 0; i < NB_JOINT; i++)
    {
        int motor_index = motor_map[msg->name[i]];
        joint_positions[motor_index] = msg->position[i];
        joint_velocity[i] = msg->velocity[i];
        joint_effort[i] = msg->effort[i];
    }

    // ROS_INFO("Motor positions :");
    // ROS_INFO("m1 = %f, m2 = %f, m3 = %f, m4 = %f, m5 = %f", joint_positions[0], joint_positions[1], joint_positions[2], joint_positions[3], joint_positions[4]);

    for (auto i = 0; i < NB_JOINT; i++)
    {
        // ROS_INFO("Motor index order: %d", motor_index);
        if (i == 0)
        {
            double curr_joint_diff = joint_positions[0] - joint_positions[1];
            joint_angles[i] = min_angles[i] + ((curr_joint_diff - pos_min_angles[i]) * (max_angles[i] - min_angles[i]) / (pos_max_angles[i] - pos_min_angles[i]));
        }
        else if (i == 1)
        {
            double curr_joint_aver = (joint_positions[0] + joint_positions[1]) / 2;
            joint_angles[i] = min_angles[i] + ((curr_joint_aver - pos_min_angles[i]) * (max_angles[i] - min_angles[i]) / (pos_max_angles[i] - pos_min_angles[i]));
        }
        else if (i > 1)
        {
            joint_angles[i] = min_angles[i] + ((joint_positions[i] - pos_min_angles[i]) * (max_angles[i] - min_angles[i]) / (pos_max_angles[i] - pos_min_angles[i]));
        }
    }

    angle_feedback.name = {"motor1", "motor2", "motor3", "motor4", "motor5"};

    for (auto i = 0; i < NB_JOINT; i++)
    {
        angle_feedback.position.push_back(joint_angles[i]);
        angle_feedback.velocity.push_back(joint_velocity[i]);
        angle_feedback.effort.push_back(joint_effort[i]);
    }

    std_msgs::Header head;
    head.stamp = ros::Time::now();
    angle_feedback.header = head;

    // ROS_WARN("Joint angles with joint limits :");
    // ROS_WARN("j1 = %f, j2 = %f, j3 = %f, j4 = %f, j5 = %f", angle_feedback.position[0], angle_feedback.position[1], angle_feedback.position[2], angle_feedback.position[3], angle_feedback.position[4]);

    pub_angles.publish(angle_feedback);

    arm_us_msg::JointLimits joint_limits_msg;

    joint_limits_msg.joint_limits = {joint_limits[0], joint_limits[1], joint_limits[2], joint_limits[3], joint_limits[4]};

    pub_gui.publish(joint_limits_msg);
}

/**
 * @brief Angle callback when in simulation mode (bypass normal callback)
 *
 */
void simulateStateCallback()
{
    sensor_msgs::JointState angle_feedback;
    angle_feedback.name = {"motor1", "motor2", "motor3", "motor4", "motor5"};
    angle_feedback.position = {0.0, 0.0, 0.0, 0.0, 0.0};

    double max_angles[NB_JOINT];
    double min_angles[NB_JOINT];
    double pos_max_angles[NB_JOINT];
    double pos_min_angles[NB_JOINT];

    for (int i = 0, j = 0; i < NB_JOINT; i++)
    {
        ros::param::get("/" + NODE_NAME + "/j" + std::to_string(i + 1) + "/pos_max_angle", pos_max_angles[i]);
        ros::param::get("/" + NODE_NAME + "/j" + std::to_string(i + 1) + "/pos_min_angle", pos_min_angles[i]);
        ros::param::get("/" + NODE_NAME + "/j" + std::to_string(i + 1) + "/max_limit", max_angles[i]);
        ros::param::get("/" + NODE_NAME + "/j" + std::to_string(i + 1) + "/min_limit", min_angles[i]);
    }

    for (auto i = 0; i < NB_JOINT; i++)
    {
        joint_angles[i] = min_angles[i] + ((joint_positions[i] - pos_min_angles[i]) * (max_angles[i] - min_angles[i]) / (pos_max_angles[i] - pos_min_angles[i]));
        angle_feedback.position[i] = joint_angles[i];
    }

    // ROS_WARN("Joint angles with joint limits :");
    // ROS_WARN("j1 = %f, j2 = %f, j3 = %f, j4 = %f, j5 = %f", angle_feedback.position[0], angle_feedback.position[1], angle_feedback.position[2], angle_feedback.position[3], angle_feedback.position[4]);

    pub_angles.publish(angle_feedback);
}

/**
 * @brief Gets and set the needed ros::Params as global variable
 *
 */
void setParams()
{
    int controlMode = -1;

    ros::param::get("/dynamixel_interface_node/global_max_vel", max_speed);
    ros::param::get("/master_node/control_mode", controlMode);

    switch (controlMode)
    {
    // Real
    case 0:
    {
        g_control_mode = ControlMode::Real;
        ROS_WARN("Started interface node in real control mode");
        break;
    }
    // Simulation
    case 1:
    {
        g_control_mode = ControlMode::Simulation;
        ROS_WARN("Started interface node in simulation control mode");
        break;
    }
    // Default
    default:
    {
        g_control_mode = ControlMode::Real;
        ROS_ERROR("Control mode parameter not read from launch file");
        break;
    }
    }

    joint_positions[0] = 0.0;
    joint_positions[1] = 0.0;
    joint_positions[2] = 0.0;
    joint_positions[3] = 0.0;
    joint_positions[4] = 0.0;
}

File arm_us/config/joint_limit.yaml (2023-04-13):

  j1:
    max_limit: 90.0
    min_limit: -90.0
    pos_max_angle: 3.273515001347957
    pos_min_angle: -9.806739176952904
  j2:
    max_limit: 180.0
    min_limit: 0.0
    pos_max_angle: 7.007991229455552
    pos_min_angle: -3.044184873559055
  j3:
    max_limit: 180.0
    min_limit: 90.0
    pos_max_angle: -0.5537670644267164
    pos_min_angle: -2.382272163586401
  j4:
    max_limit: 720.0
    min_limit: -720.0
    pos_max_angle: 7.06
    pos_min_angle: -18.08
  j5:
    max_limit: 90.0
    min_limit: -90.0
    pos_max_angle: 2.1353
    pos_min_angle: -0.928

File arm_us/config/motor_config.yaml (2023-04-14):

loop_rate: 50                      # desired rate for joint state updates. actual rate may be less depending on number
                                  # of dynamixels on each port
control_mode: velocity            # control mode, either 'position', 'velocity', or 'effort'
disable_torque_on_shutdown: true  # with this enabled the motors will switch off when the controller closes
ignore_input_velocity: false      # ignore input velocity commands in position mode (no profile velocity)
diagnostics_rate: 1               # rate to publish diagnostic information
dataport_rate: 1                  # rate to read from dynamixel external dataports

# The below values are used as global defaults and are applied for each servo unless overridden in the entry for the servo below
global_max_vel: 1 # 4.5           # maximum joint speed (rad/s) (in position or velocity control)
global_torque_limit: 0.5          # maximum motor torque for all modes, given as a fraction of rated max (0-1)

# PORT AND SERVO CONFIGURATIONS
ports:

  # PORT LIST
  - name: Port_1               # name for this port in config
    device: /dev/ttyACM0       # serial device this port will communicate on
    baudrate: 57600            # baudrate in use
    use_legacy_protocol: false # wether to use new 2.0 protocol (false) or legacy 1.0 protocol (true)
    group_read_enabled: true   # specify whether to use group comms for reading
    group_write_enabled: true  # specify whether to use group comms for writing
    servos:
        # SERVO LIST FOR THIS PORT
        - id: 50
          joint_name: motor5
          zero_pos: 2048
          min_pos: 0
          max_pos: 4095

        - id: 40
          joint_name: motor4
          zero_pos: 2048
          min_pos: 0
          max_pos: 4095

        - id: 30
          joint_name: motor3
          zero_pos: 2048
          min_pos: 0
          max_pos: 4095

        - id: 20
          joint_name: motor2
          zero_pos: 2048
          min_pos: 0
          max_pos: 4095

        - id: 10
          joint_name: motor1
          zero_pos: 2048
          min_pos: 0           
          max_pos: 4095

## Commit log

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2023-01-21 adding first solidWork assembly
    [ARMUS-100-000.SLDASM, ARMUS-100-002.SLDPRT]
2023-01-24 add shoulder support v1
    [ARMUS-100-000.SLDASM, ARMUS-100-005.SLDASM, ARMUS-100-005.stp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]
2023-01-26 Multiples changes
    - Fixed CMake
    - Added .yaml config for controller and both XL430 motors
    - Added launchfile for controller node
    - Added publisher to motor
    [controller_config.yaml]
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2023-01-31 Added motor-shaft coupling adapter
    [ARMUS-100-007.SLDPRT]
2023-01-31 Added STL
    Didn't follow for whatever reason
2023-01-31 - generation des fichies pour print
    [ARMUS-100-001.3MF, ARMUS-100-002.3MF, ARMUS-100-003.3MF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]
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2023-02-01 Sprint 1 - ARMUS-200-001
    [ARMUS-200-001.SLDPRT]
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2023-02-04 Continued REV2 of the shoulder
    [ARMUS-200-000.SLDASM, ARMUS-REV2-000.SLDASM, ARMUS-REV2-001.SLDPRT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]
2023-02-04 CleanUp and fix naming
    [ARMUS-REV2-000.SLDASM, ARMUS-REV2-001.SLDPRT, ARMUS-REV2-002.SLDPRT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]
2023-02-05 Ajout support pour charges axiales
    [ARMUS-REV2-000.SLDASM, ARMUS-REV2-001.SLDPRT, ARMUS-REV2-100.SLDASM]
2023-02-06 boite avec hub pour fixer la bevel gear (main gear)
    [ARMUS-REV2-001.SLDPRT, ARMUS-REV2-003.SLDPRT, ARMUS-REV2-200.SLDASM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]
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2023-02-07 box to support bevel gear prob fnished
    [ARMUS-REV2-003.SLDPRT, ARMUS-REV2-200.SLDASM]
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2023-02-07 Shaft Motor Support Modification
    [ARMUS-REV2-004.step.SLDPRT]
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2023-02-08 -Update motor support and gear distance
    [ARMUS-REV2-000.SLDASM, ARMUS-REV2-001.SLDPRT, ARMUS-REV2-003.SLDPRT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]
2023-02-08 make the support adapt to the assembly
    [ARMUS-REV2-000.SLDASM, ARMUS-REV2-001.SLDPRT, ARMUS-REV2-004.step.SLDPRT]
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2023-02-08 adding of hole to put bolt into motors
    [ARMUS-REV2-000.SLDASM, ARMUS-REV2-001.SLDPRT, ARMUS-REV2-004.step.SLDPRT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]
2023-02-08 main gear (bevel gear) XXX
    [ARMUS-REV2-XXX.SLDPRT]
2023-02-09 Fused gears and made cura slice
    [ARMUS-REV2-100.SLDPRT, ARMUS-REV2-300.SLDASM, ARMUS-REV2-301.SLDPRT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]
2023-02-09 Slicing and optimizing for print
    [1x ARMUS-REV2-003.STL, ARMUS-REV2-000.SLDASM, ARMUS-REV2-001.SLDPRT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]
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2023-02-09 second try add bore_set_screw_D_bore
    [bore_set_screw_D_hub.SLDASM, bore_set_screw_D_hub.SLDPRT]
2023-02-09 Fix gear relations
    [ARMUS-REV2-000.SLDASM, ARMUS-REV2-003.SLDPRT, ARMUS-REV2-004.SLDPRT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]
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2023-02-09 gear_moteur as a part
    [gear_moteur.SLDPRT]
2023-02-09 Fixed naming and subassemblies relations
    [ARMUS-REV2-000.SLDASM, ARMUS-REV2-001.SLDPRT, ARMUS-REV2-003.SLDPRT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]
2023-02-10 Did last before print modifications and did cura sliced
    [1x ARMUS-REV2-003.STL, 1x ARMUS-REV2-201.STL, 2x ARMUS-REV2-501.STL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]
2023-02-15 Major Shoulder Support and assembly modifications
    [585446.step.SLDPRT, 585580.step.SLDPRT, ARMUS-REV2-000.SLDASM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]
2023-02-15 Fixed naming
    [ARMUS-REV4-001.SLDPRT, ARMUS-REV4-003.SLDPRT, ARMUS-REV4-004.SLDPRT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]
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2023-02-15 second try for dxf
    [Etat déplié - ARMUS-REV4-001_V2.DXF]
2023-02-17 GUI subscriber in master node to control motors
    [ARMUS-100-000.SLDASM, ARMUS-100-001.SLDPRT, ARMUS-100-002.SLDPRT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]
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2023-02-17 Upper Arm Shoulder Joint
    [ARMUS-200-000.SLDASM, ARMUS-200-003.SLDPRT]
2023-02-18 Upper Arm Print Modification
    [ARMUS-200-000.SLDASM, ARMUS-202-001.SLDPRT, ARMUS-202-002.SLDPRT]
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2023-02-19 ajusting of the motor support for shoulder
    [ARMUS-REV2-000.SLDASM, ARMUS-REV2-004.SLDPRT, ARMUS-REV2-005.SLDPRT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]
2023-02-19 CADs + STL of the spacers to print (2x each)
    [ARMUS-REV4-006-08.SLDPRT, ARMUS-REV4-006-08.STL, ARMUS-REV4-006-09.SLDPRT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]
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2023-02-20 Contol xm430 motors with joysticks
    [controller_config.yaml]
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2023-02-20 Control motors with Gui
    [controller_config.yaml]
2023-02-21 Slicing spacers + new supports for motors
    [ARMUS-REV4-003.STL, ARMUS-REV4-004.STL]
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2023-02-21 Shoulder REV5 modification and slice
    [ARMUS-REV4-001_V2.SLDPRT, ARMUS-REV4-002.SLDPRT, ARMUS-REV4-003.SLDPRT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]
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2023-02-23 Made new Motor Coupler (V3)
    [ARMUS-REV4-002.SLDPRT, ARMUS-REV4-002_V3.STL]
2023-02-25 Wrist - preliminary design
    [ARMUS-500-000.SLDASM, ARMUS-500-001.SLDPRT, ARMUS-500-002.SLDPRT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]
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2023-03-01 Wrist preliminary design - higher base
    [ARMUS-500-000.SLDASM, ARMUS-500-001.SLDPRT, ARMUS-500-003.SLDPRT]
2023-03-01 ajout des pièce pour l'assemblage du coude
    [ARMUS-200-000.SLDASM, ARMUS-200-004.SLDPRT, ARMUS-201-003.SLDPRT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]
2023-03-02 Wrist with lady Susan bearing
    [ARMUS-500-000.SLDASM, ARMUS-500-001.SLDPRT, ARMUS-500-003.SLDPRT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]
2023-03-03 add of support for humerus motors
    [ARMUS-200-000.SLDASM, ARMUS-202-002.SLDPRT, SymétrieARMUS-202-002.SLDPRT]
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2023-03-03 CADed amazon lady suzan Bearing
    [Lady Suzan.SLDPRT]
2023-03-04 Revert "Wrist with lady Susan bearing"
    This reverts commit 412b4896b0f98d06493c850aec47e6817995b997.
    [ARMUS-500-000.SLDASM, ARMUS-500-001.SLDPRT, ARMUS-500-003.SLDPRT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]
2023-03-06 Wrist with flat head screws 6mm
    [ARMUS-500-000.SLDASM, ARMUS-500-001.SLDPRT, ARMUS-500-003.SLDPRT]
2023-03-07 Gear modification and ajustement for the helbow
    [ARMUS-200-000.SLDASM, ARMUS-201-003.SLDPRT, ARMUS-202-002.SLDPRT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]
2023-03-08 Shafts ajusting for the helbow
    [ARMUS-200-000.SLDASM, ARMUS-202-002.SLDPRT, Bearing.step.SLDPRT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]
2023-03-08 Support add for the gear shaft(helbow)
    [ARMUS-200-000.SLDASM, ARMUS-202-002.SLDPRT, Pignon 24T.SLDPRT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]
2023-03-08 Communication betwene master and graph
    [controller_config.yaml]
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2023-03-11 forearm preliminary design with reinforcement
    [ARMUS-500-000.SLDASM, ARMUS-500-001.SLDPRT, ARMUS-500-003.SLDPRT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]
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2023-03-15 cad for the potentio on the elbow
    [potentio_coude.SLDPRT]
2023-03-15 ForeArm Redesign (Sorry Amy-Lou :( )
    [ARMUS-200-000.SLDASM, ARMUS-202-002.SLDPRT, ARMUS-500-000.SLDASM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]
2023-03-15 adding STL of the forearm
    [ARMUS-500-001.STL, ARMUS-500-003.STL, ARMUS-500-004.STL]
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2023-03-22 Solidification off motor support on the upper arm
    [ARMUS-200-000.SLDASM, ARMUS-202-002.SLDPRT, ARMUS-202-002.STL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]
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2023-04-07 Cleaned up code, added comments,
    Inverse kinematics potentially working in real mode
    [motor_config.yaml]
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2023-04-07 Completed motor translator
    Added security for motor deco and limits
    [motor_config.yaml]
2023-04-07 Simulation kind of working with interface
    Working in joint kinda ... Not in cartesian
    [motor_config.yaml]
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2023-04-08 Speed limiter factor correction
    for accuracy in cartesian mode
    [motor_translator.cpp]
2023-04-09 Corrections to motor translator
    #include "ArmUs.hpp" not working and not needed ???
    Max speed get param changed to work
    [motor_translator.cpp]
2023-04-09 Reversed comparation operator in speed limiter
    [motor_translator.cpp]
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2023-04-13 On a win pour vrais
    Fix la cinematique inverse (un - et un + inversé)
    Reactiver la limit de joint
    Updater les dimensions physique du bras
    Ajouter démultiplication des moteurs
    Fait un rosparam dump des calibs
    [motor_calib.yaml]
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2023-04-17 Modified message files
    Modified message files :
    - GraphInfo.msg
    - JointLimits.msg
    Instead of having fixed number of elements, accept any number of elements to pass std::vector<double> that is implicitely casted to const boost::array<double>
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
